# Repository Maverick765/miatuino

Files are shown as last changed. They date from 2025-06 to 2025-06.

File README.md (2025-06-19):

# Miatuino ECU NA6 PNP


MiatuinoはSpeeduinoをベースとしたNA6ロードスター専用ECUプロジェクトです。

Speeduino MX-5 PNPモデルをベースとし、部品の入手性、組み立てやすさなどを改善しました。

基本的な技術情報については公式のWikiを参照してください。
https://wiki.speeduino.com

また、部品に関してはできる限り日本国内で入手しやすいものにしています。国内で入手できないものはAliexpressやLCSCで入手可能です。

---

## 対応車種

- 車種：ユーノス・ロードスター（NA6CE）
- 年式：1989年〜1995年
- エンジン：1.6L B6ZE(RS)

注意：NA8には対応していません。

---

## Speeduinoからの変更点

- Arduino Mega2560をMega2560 Proに変更
- SMD部品を減らし、手はんだで組み立てやすいように変更
- A/C制御回路の追加
- 電源回路をROHM製のDC-DCコンバータBP5293-50に変更
- MAPセンサをBOSCH製0 281 002 593に変更

---

## 注意事項

- 仕様はほぼSpeeduinoと同様です。詳細仕様は [Speeduino公式Wiki](https://wiki.speeduino.com/) を参照してください。
- 純正には**吸気温センサー（IAT）が存在しない**ため、追加設置が必須です。
- ノック制御、スピードセンサーなどには非対応です。

---

## ECUの組み立てと取付に必要なもの

- Miatuino基板  
リポジトリ内のGerberファイルを利用。
- 実装用部品  
リポジトリ内の部品表を参照。
- 吸気温センサー(IAT)  
品番：25036751  
エアフロメーターを外したカプラに接続します。  
Aliexpressなどで入手可能
- 吸気温センサー用カプラ  
Aliexpressで「7pin Automotive Connector」などと検索すれば見つかります。
- スロットルポジションセンサー(TPS)  
品番：0280122001  
カプラの形状と配線が純正と同じため、そのまま利用できます。  
Aliexpressなどで入手可能。
- スロットルポジションセンサー用マウントアダプター  
リポジトリ内の.stlファイルを利用。  
3Dプリンタで出力するか、3Dプリントサービスを利用してください。  
.stlファイルは以下のページからも入手可能です。  
[1.6 Miata Kia type tps adapter M5 nuts](https://www.thingiverse.com/thing:4611603)
- MAPセンサー  
0 281 002 593  
Aliexpressなどで入手可能。
- MAPセンサー用カプラー  
品番：1928403966  
Aliexpressなどで入手可能。
- 基板用ケース  
基板のサイズは100mm x 100mmです。適当なサイズのアルミケースに入れます。
- 基板用USB Type Cコネクタ  
ケース内のMega 2560 Proと接続するためのパネルマウントのType Cコネクタ。
- 内径4.5mmのホース   
3m程度。キジマのガソリンホースがおススメです。
- TunerStudio  
[公式ページ](https://www.efianalytics.com/TunerStudio/)から入手可能。
- SpeedyLoader  
[公式ページ](https://speeduino.com/home/support/downloads)から入手可能。

---

## 製作

基本的にはKiCADのプロジェクトや部品表を見ながらはんだ付けすればOKです。
MAPセンサーは基板の3ピンコネクタにカプラを介して取り付けます。

---

## ファームウェアの書き込み

SpeedyLoaderを利用してファームウェアを書き込みます。
[SpeedyLoaderの公式マニュアル](https://wiki.speeduino.com/en/Installing_Firmware)を参考にしてください。

また、書き込みが完了したらbase tuneをダウンロードしておきます。

---

## 取付手順

### スロットルポジションセンサーを交換する

純正のスロットルポジションセンサーを外し、新しいスロットルポジションセンサーをアダプターを利用して取り付けます。

なお、純正のセンサーを取り外すには、スロットルボディーを外す必要があります。
(純正のセンサーを破壊すればスロットルボディーを外さずに新しいセンサーを取り付けることも可能ですがおススメしません)

### エアフロメーターのカプラを外して吸気温センサーを取り付ける

エアフロメータにつながっている7ピンのカプラを外し、吸気温センサを取り付けます。

### ST-SIGのヒューズを外す

エンジンルーム内の運転席側のヒューズボックスを開け、ST-SIGのヒューズを外します。
なお、Miatuinoを利用する場合、このヒューズは常に外したままにしておく必要があります。

_ST-SIGのヒューズは、セルモーターを回している間、一時的に燃料ポンプを動かすための電源が来ているヒューズです。_
_純正状態のNA6では、燃料ポンプの電源ON/OFFをフラップ式のエアフロメータの中にある機械式の接点で行っています。つまり、エンジンが回って負圧が発生している状態でないと燃料ポンプは作動しません。_
_エンジン始動時は負圧が弱く、この接点が動かないため、一時的に燃料ポンプに電源を供給する必要があります。その電源が来ているのがST-SIGのヒューズです。_
_Miatuinoでは、エアフロメータの配線を流用して燃料ポンプの制御を行うことになりますが、この時、ST-SIGのヒューズを残したままにしていると、キーを回したときに基板のドライバICに電流が逆流し、基板が焼けます。_

### 純正ECUを取り外す

助手席側スカッフプレート、一部のトリムを外してカーペットをめくります。
スチールのカバーパネルを外すと、ステーで固定されたECUが見えるので取り外し、カプラーを外します。

### MAPセンサーへつなぐホースを通す

MiatuinoではDジェトロニック方式になるため、インテークマニホールドの負圧をホースでECUまで接続する必要があります。
純正のインテークマニホールドには、ゴムキャップが付いた使われていない負圧取り出しニップルがあるので、それを利用します。
また、ロードスターのエンジンルーム隔壁にはゴム栓でメクラされた穴があるので、その栓を外してホースを通します。

カーペットをめくっている間に、エンジンルーム側からホースを送り、室内側の足元まで届かせます。
室内と反対側のホースの先をインマニにあるニップルに取り付けます。

### Miatuinoを取り付ける

純正ECUを取り外したカプラと、先ほど通したホースをMiatuinoに繋ぎます。
ECUのセッティングやトラブルシューティングのためにも、ECUは元の場所に戻さず、助手席足元に転がすなりしておきます。
ECU底面に面ファスナーのテープを取り付け、内装に張り付けておくのもおすすめです。

---

## セットアップ手順

PCとMiatuinoをUSBケーブルで接続し、PCでTuner Studioを起動し、初期データの書き込みと各種センサーのキャリブレーションを行います。

#### 初期データの書き込み

SpeedyLoaderからダウンロードしたbase tuneを書き込みます。

[File] -> [Load Tune(MSQ)]を選択して、SpeedyLoaderでからダウンロードしたbase tuneを書き込みます。

#### TPSのキャリブレーション

[Tools] -> [Calibrate TPS]を選択します。

正しくTPSが接続されていれば、アクセルペダルを踏めば値が変化することを確認できます。

まずはアクセルを完全に戻した状態で[Closed throttle ADC Count]の右の[Get Current]をクリックして、スロットル全閉時の値を取得します。
次に、アクセルを完全に踏み込んだ状態で[Full throttle ADC Count]の右の[Get Current]をクリックして、スロットル前回時の値を取得します。
完了したら[Accept]をクリックします。

この際、センサーの極性(全開で0Vか、全閉で0Vか)で警告が出ることがありますが、そのまま進めればSpeeduino側で勝手に極性を変更してくれます。

#### 水温センサーのキャリブレーション

[Tools] -> [Calibrate Tempereture Sensor]を選択します。

[SensorTable]のプルダウンから[Coolant Tempereture Sensor]を選択します。

[Table Input Solution]が3 Point Therm Generatorになっていることを確認します。

[Common Sensor Values]のプルダウンから[RX7_CLT(S4&S5)]を選択します。

[Write to Controller]をクリックして完了したら[Close]をクリックします。

#### 吸気温センサーのキャリブレーション

[Tools] -> [Calibrate Tempereture Sensor]を選択します。

[SensorTable]のプルダウンから[Air Tempereture Sensor]を選択します。

[Table Input Solution]が3 Point Therm Generatorになっていることを確認します。

[Common Sensor Values]のプルダウンから[RX7_AFM(S5 in AFM)]を選択します。

[Write to Controller]をクリックして完了したら[Close]をクリックします。

#### O2センサーの設定

[Tuning] -> [AFR/O2]を選択します。

純正のO2センサーを利用する場合、[Sensor Type]に[Narrow Band]を指定します。

完了したら[Burn]をクリックして[Close]をクリックします。

純正のO2センサーを利用する場合はこれで完了ですが、社外のワイドバンドセンサーを付けている場合はキャリブレーションを行う必要があります。

[Tools] -> [Calibrate AFR Sensor]を選択します。

[EGO Sensor]のプルダウンメニューから、利用しているセンサーのメーカーを選択します。

[Write to Controller]をクリックして完了したら[Close]をクリックします。

---

## 関連リンク

- [Speeduino 公式サイト（英語）](https://speeduino.com/)
- [Speeduino Wiki（英語）](https://wiki.speeduino.com/en/boards/MX5_PNP)
- [TunerStudio ダウンロードページ](https://www.efianalytics.com/TunerStudio/)
- [Speedy Loader ダウンロードページ](https://speeduino.com/home/support/downloads)
- [1.6 Miata Kia type tps adapter M5 nuts](https://www.thingiverse.com/thing:4611603)

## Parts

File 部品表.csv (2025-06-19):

Reference | Value | URL | 数量 | 備考
C1,C3 | 10uF | https://akizukidenshi.com/catalog/g/g117897/ | 2
C2,C6,C7,C8,C11,C12,C13,C17,C18,C19,C20,C21,C22,C23 | 0.1uF | https://akizukidenshi.com/catalog/g/g117059/ | 14
C4 | 22uF | https://akizukidenshi.com/catalog/g/g108156/ | 1
C5 | 470pf | https://akizukidenshi.com/catalog/g/g108130/ | 1
C9,C10,C14,C15,C16 | 0.22uF | https://akizukidenshi.com/catalog/g/g103096/ | 5
D1 | 1N5818 | https://www.lcsc.com/product-detail/Schottky-Diodes_STMicroelectronics-1N5818_C5220773.html?s_z=n_1N5818 | 1
D2 | SBM245L | https://akizukidenshi.com/catalog/g/g117439/ | 1
D3 | LED Power | https://akizukidenshi.com/catalog/g/g111637/ | 1
D4,D5,D6,D8,D13,D14,D19,D20 | D | https://akizukidenshi.com/catalog/g/g100941/ | 8
D7 | LED Fuel | https://akizukidenshi.com/catalog/g/g111577/ | 1
D9,D10,D11,D12,D15,D16,D17,D18 | LED Inj, LED Ign | https://akizukidenshi.com/catalog/g/g112607/ | 8
J1 | Connector_174917-1 | https://www.lcsc.com/product-detail/Wire-To-Board-Connector_TE-Connectivity-174917-1_C5166285.html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 | 1 | 入手性にやや難あり。 「174917-1」で検索すると見つかるかも。
J2 | Conn_01x03_Socket | https://akizukidenshi.com/catalog/g/g112816/ | 1
R1,R6,R7,R8,R12,R13,R14,R44,R45 | 470R | https://akizukidenshi.com/catalog/g/g125471/ | 9
R2,R23 | 10k | https://akizukidenshi.com/catalog/g/g125103/ | 2
R3 | 120R | https://akizukidenshi.com/catalog/g/g125121/ | 1
R4,R9,R15,R16,R20,R21,R22,R25,R26,R28,R29,R32,R33,R34,R35,R38,R39,R40,R41,R46 | 1k | https://akizukidenshi.com/catalog/g/g125102/ | 19
R5 | 3.9k | https://akizukidenshi.com/catalog/g/g125392/ | 1
R10,R11,R27 | 2.49k | https://jp.rs-online.com/web/p/through-hole-resistors/7549032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 | 3
R17,R18 | 220R | https://akizukidenshi.com/catalog/g/g125221/ | 2
R19 | 22K | https://akizukidenshi.com/catalog/g/g125223/ | 1
R24,R30,R31,R47,R48 | 100k | https://akizukidenshi.com/catalog/g/g125104/ | 7
R36,R37,R42,R43 | 3.3k | https://akizukidenshi.com/catalog/g/g125332/ | 4
RN1,RN2 | 100k | https://lcsc.com/product-detail/image/A05-104JP_C11398.html
RN3 | 3k | https://lcsc.com/product-detail/image/A05-302JP_C56024.html | 1
RV1 | Varistor | https://lcsc.com/product-detail/Varistors_RUILON-Shenzhen-Ruilongyuan-Elec-14D220K_C43370767.html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 | 1
SW1 | SW_Slide | https://akizukidenshi.com/catalog/g/g115643/ | 1
U1 | Mega 2560 Pro | Mega 2560 Pro | 1 | Aliexpressなどで入手可能。
U2 | IC_Automotive_MC33814 | https://lcsc.com/product-detail/Power-Management-Specialized_NXP-Semicon-MC33814AER2_C729078.html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 | 1
U3 | BP5293-50 | https://akizukidenshi.com/catalog/g/g111188/ | 1
U4 | KP234XTMA1 | https://www.lcsc.com/product-detail/Pressure-Sensors_Infineon-Technologies-KP234XTMA1_C3239348.html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 | 1
U5 | SP720 | https://www.lcsc.com/product-detail/ESD-and-Surge-Protection-TVS-ESD_Littelfuse-SP720ABG_C5299847.html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 | 1
U6,U8,U9,U11 | VNLD5090 | https://www.lcsc.com/product-detail/Power-Distribution-Switches_STMicroelectronics-VNLD5090TR-E_C222209.html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 | 4
U7 | VN5160S-E | https://www.lcsc.com/product-detail/Power-Distribution-Switches_STMicroelectronics-VN5160S-E_C262998.html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 | 1
U10,U12 | TC4424A | https://www.lcsc.com/product-detail/Gate-Drivers_Microchip-Tech-TC4424AVOA_C636876.html?s_z=n_TC4424A | 2
U13,U14 | TLP241A | https://akizukidenshi.com/catalog/g/g111516/ | 2

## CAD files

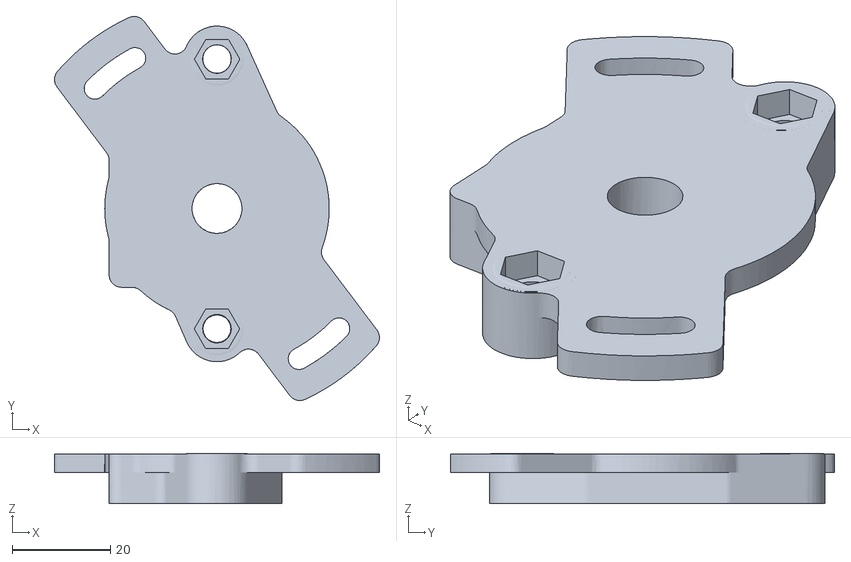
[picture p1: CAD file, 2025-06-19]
1.6_Miata_Kia_Tps_Adapter_M5.stl
66.3 x 78.3 x 10.2

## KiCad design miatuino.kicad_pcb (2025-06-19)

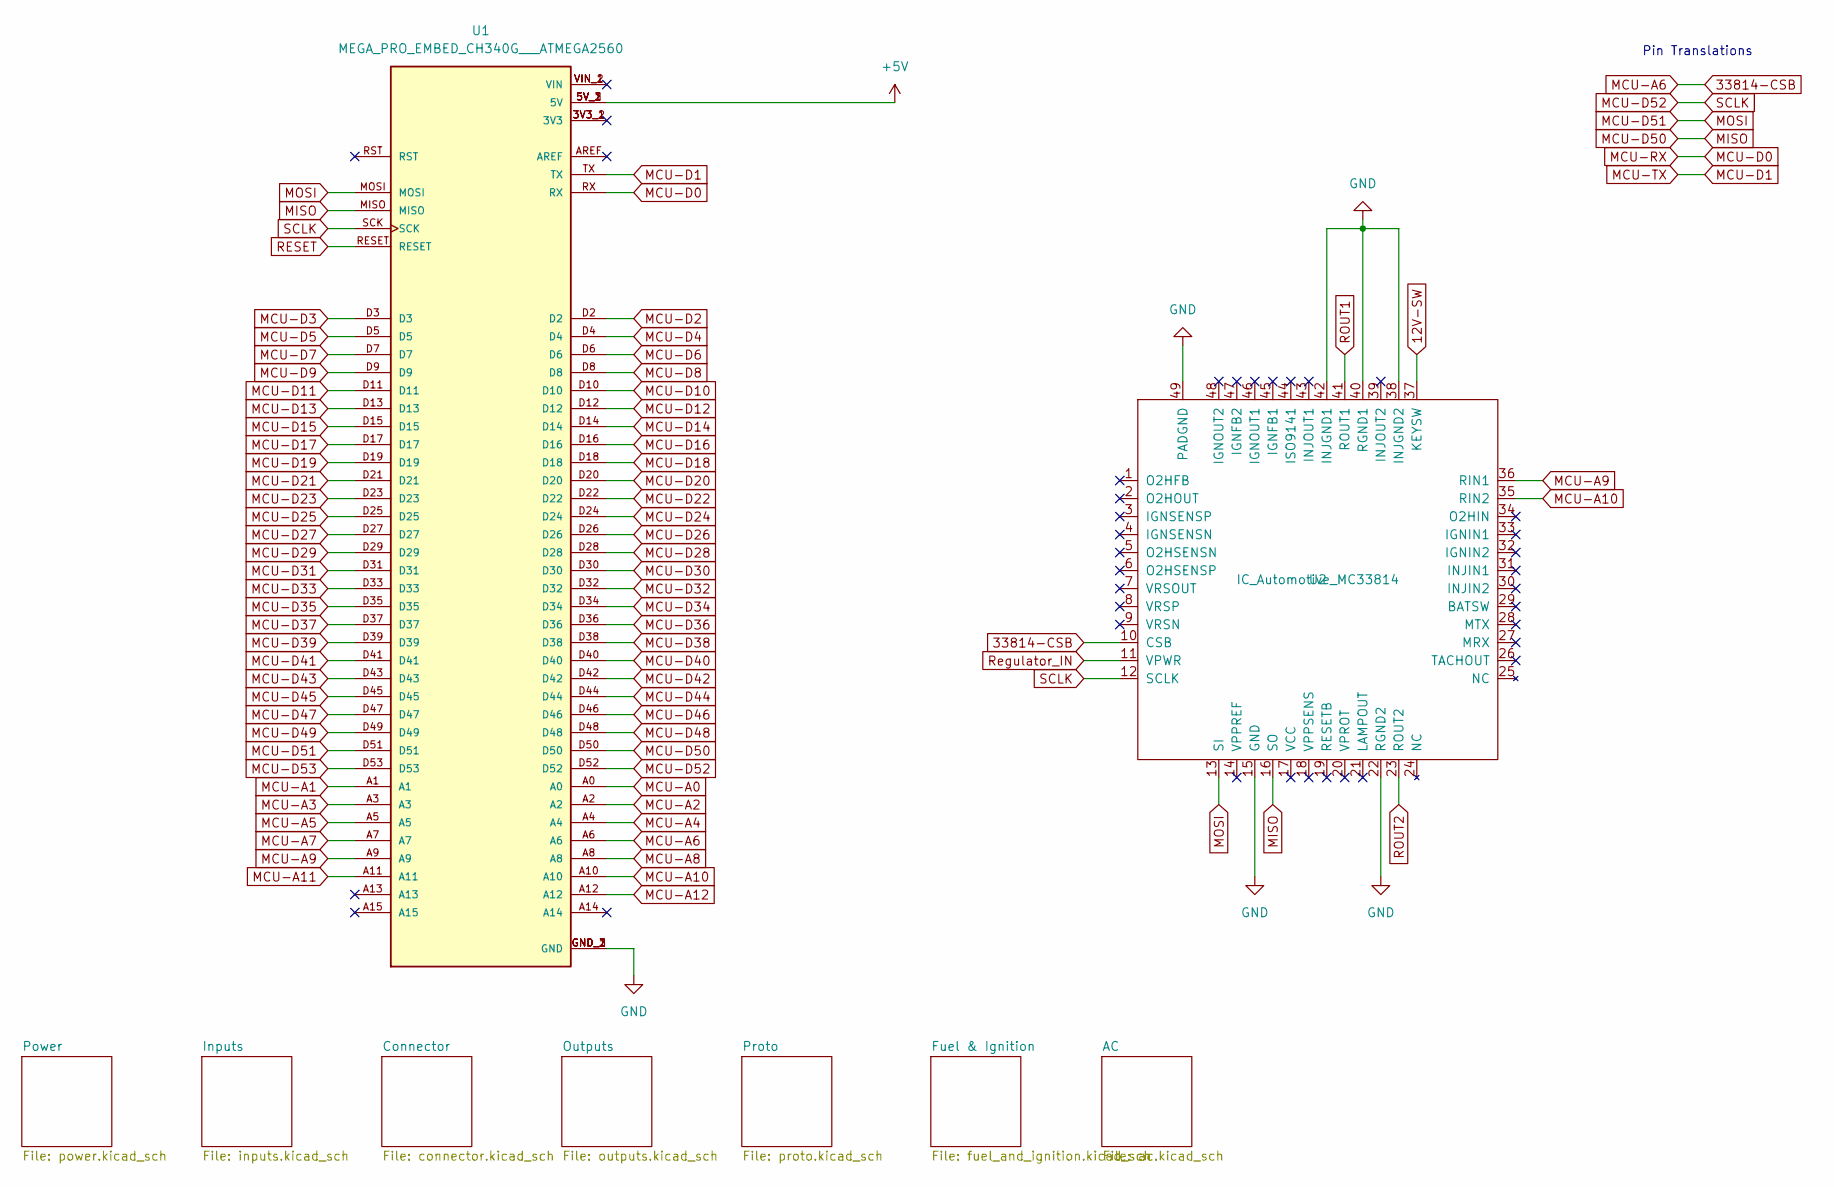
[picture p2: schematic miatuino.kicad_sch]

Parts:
U1: MEGA_PRO_EMBED_CH340G___ATMEGA2560; Arduino Mega Pro; PARTREV 12/May/2017
U2: IC_Automotive_MC33814; LQFP-48-1EP_7x7mm_P0.5mm_EP3.6x3.6mm_ThermalVias; Manufacturer_Part_Number MC33814

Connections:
12V-SW: U2.37 (KEYSW); also elsewhere on the board
33814-CSB: U1.A6, U2.10 (CSB)
+5V: U1.5V_1 (5V), U1.5V_2 (5V), U1.5V_3 (5V); also elsewhere on the board
ADC-Clamp-1: U1.A0; also elsewhere on the board
ADC-Clamp-2: U1.A1; also elsewhere on the board
ADC-Clamp-3: U1.A2; also elsewhere on the board
ADC-Clamp-4: U1.A3; also elsewhere on the board
ADC-Clamp-5: U1.A4; also elsewhere on the board
ADC-Clamp-11: U1.D12; also elsewhere on the board
ADC-Clamp-13: U1.D18; also elsewhere on the board
ADC-Clamp-14: U1.D19; also elsewhere on the board
GND: U1.GND_1 (GND), U1.GND_2 (GND), U1.GND_3 (GND), U2.15 (GND), U2.22 (RGND2), U2.38 (INJGND2), U2.40 (RGND1), U2.42 (INJGND1), U2.49 (PADGND); also elsewhere on the board
MCU-A5: U1.A5; also elsewhere on the board
MCU-A7: U1.A7
MCU-A8: U1.A8
MCU-A9: U1.A9, U2.36 (RIN1)
MCU-A10: U1.A10, U2.35 (RIN2)
MCU-A11: U1.A11
MCU-A12: U1.A12; also elsewhere on the board
MCU-D0: U1.RX; also elsewhere on the board
MCU-D1: U1.TX; also elsewhere on the board
MCU-D2: U1.D2; also elsewhere on the board
MCU-D3: U1.D3
MCU-D4: U1.D4; also elsewhere on the board
MCU-D5: U1.D5
MCU-D6: U1.D6
MCU-D7: U1.D7
MCU-D8: U1.D8; also elsewhere on the board
MCU-D9: U1.D9; also elsewhere on the board
MCU-D10: U1.D10; also elsewhere on the board
MCU-D11: U1.D11; also elsewhere on the board
MCU-D13: U1.D13
MCU-D14: U1.D14
MCU-D15: U1.D15
MCU-D16: U1.D16
MCU-D17: U1.D17
MCU-D20: U1.D20; also elsewhere on the board
MCU-D21: U1.D21
MCU-D22: U1.D22
MCU-D23: U1.D23
MCU-D24: U1.D24
MCU-D25: U1.D25
MCU-D26: U1.D26
MCU-D27: U1.D27
MCU-D28: U1.D28
MCU-D29: U1.D29
MCU-D30: U1.D30
MCU-D31: U1.D31
MCU-D32: U1.D32; also elsewhere on the board
MCU-D33: U1.D33; also elsewhere on the board
MCU-D34: U1.D34
MCU-D35: U1.D35; also elsewhere on the board
MCU-D36: U1.D36
MCU-D37: U1.D37; also elsewhere on the board
MCU-D38: U1.D38
MCU-D39: U1.D39; also elsewhere on the board
MCU-D40: U1.D40
MCU-D41: U1.D41; also elsewhere on the board
MCU-D42: U1.D42
MCU-D43: U1.D43
MCU-D44: U1.D44; also elsewhere on the board
MCU-D45: U1.D45
MCU-D46: U1.D46; also elsewhere on the board
MCU-D47: U1.D47
MCU-D48: U1.D48
MCU-D49: U1.D49; also elsewhere on the board
MCU-D50: U1.D50, U1.MISO, U2.16 (SO)
MCU-D51: U1.D51, U1.MOSI, U2.13 (SI)
MCU-D52: U1.D52, U1.SCK, U2.12 (SCLK)
MCU-D53: U1.D53
RESET: U1.RESET; also elsewhere on the board
ROUT1: U2.41 (ROUT1); also elsewhere on the board
ROUT2: U2.23 (ROUT2)
Regulator_IN: U2.11 (VPWR); also elsewhere on the board

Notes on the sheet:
Pin Translations

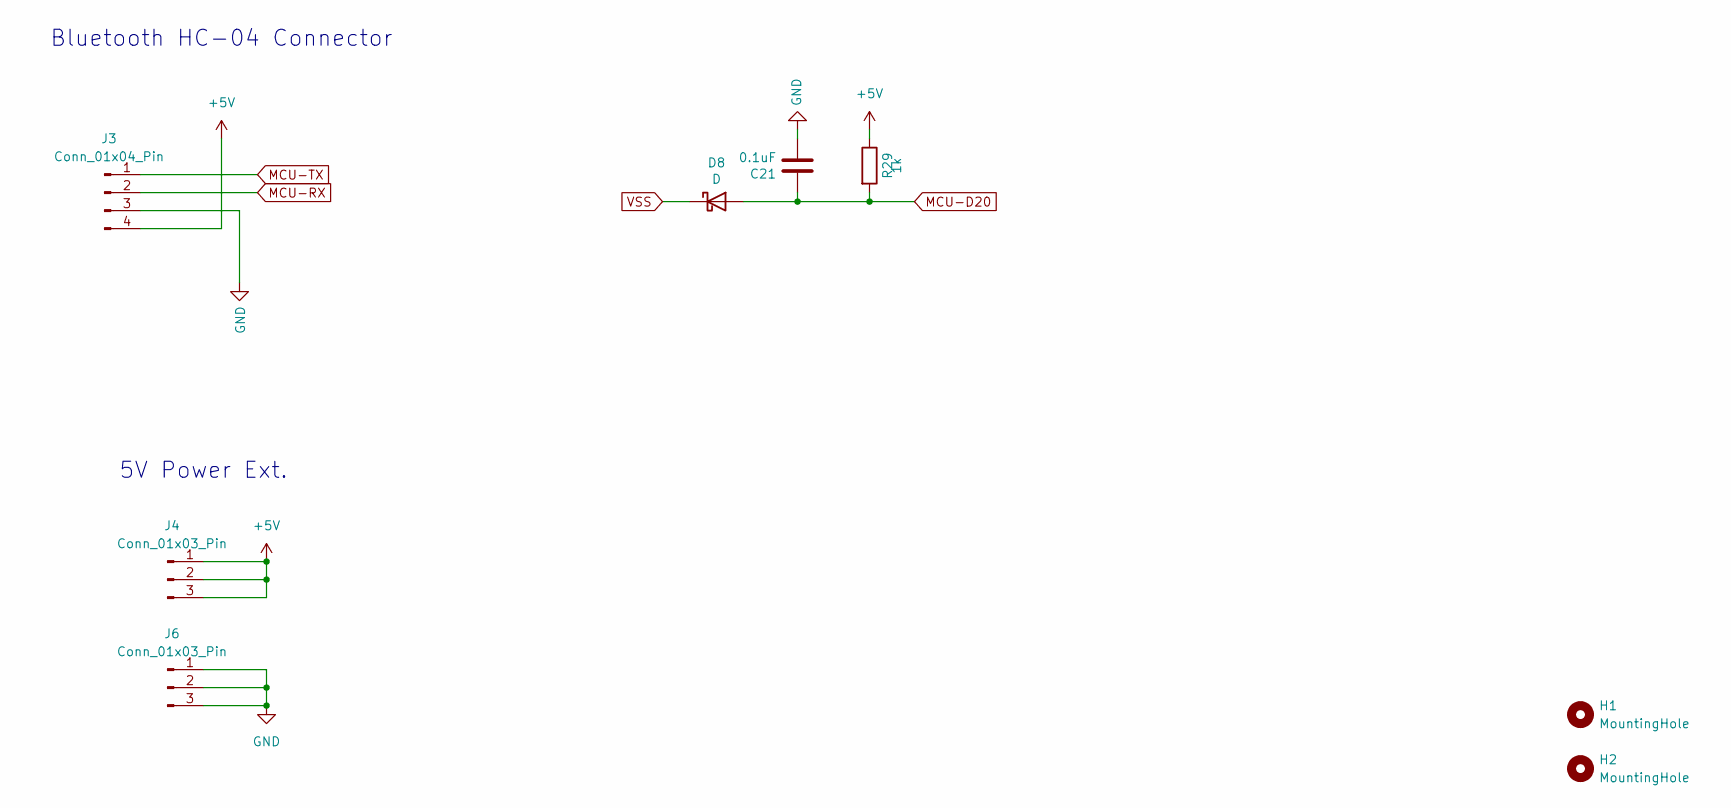
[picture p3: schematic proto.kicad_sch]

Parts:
C21: 0.1uF; C_Disc_D4.7mm_W2.5mm_P5.00mm; Manufacturer_Part_Number CC0805KRX7R9BB104; Digikey Part Number 311-1140-1-ND
D8: D; D_T-1_P5.08mm_Horizontal; Manufacturer_Part_Number 1N4448WX-TP; Digikey Part Number 1N4448WXTPMSCT-ND
H1, H2: MountingHole; MountingHole_3.2mm_M3_DIN965_Pad
J3: Conn_01x04_Pin; PinSocket_1x04_P2.54mm_Vertical
J4, J6: Conn_01x03_Pin; PinHeader_1x03_P2.54mm_Vertical
R29: 1k; R_Axial_DIN0207_L6.3mm_D2.5mm_P7.62mm_Horizontal; Manufacturer_Part_Number RC0805FR-071KL; Digikey Part Number 311-1.00KCRCT-ND

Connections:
+5V: J3.4, J4.1, J4.2, J4.3, R29.1; also elsewhere on the board
GND: C21.2, J3.3, J6.1, J6.2, J6.3; also elsewhere on the board
MCU-D0: J3.2; also elsewhere on the board
MCU-D1: J3.1; also elsewhere on the board
MCU-D20: C21.1, D8.2 (A), R29.2; also elsewhere on the board
VSS: D8.1 (K); also elsewhere on the board

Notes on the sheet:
Bluetooth HC-04 Connector
5V Power Ext.

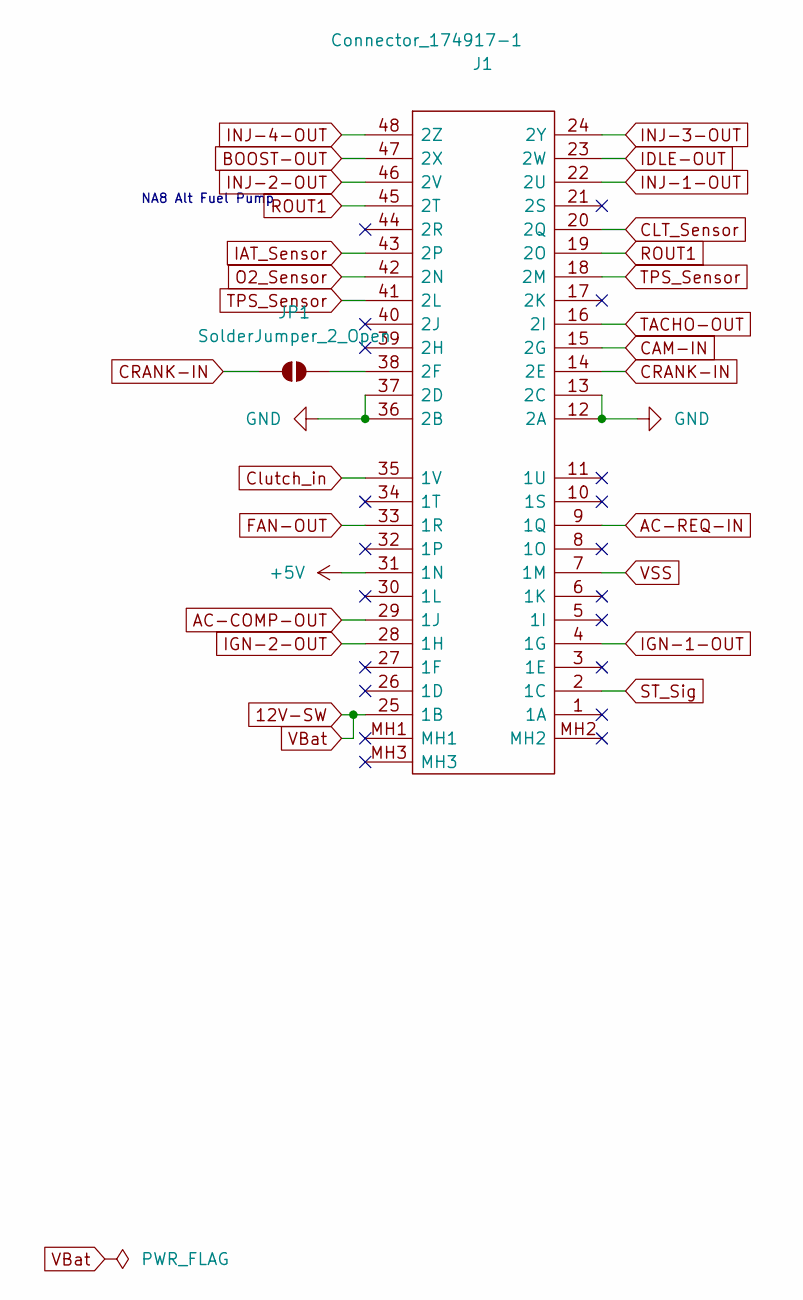
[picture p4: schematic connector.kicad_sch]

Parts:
J1: Connector_174917-1; 1749171; Manufacturer_Part_Number 174917-1
JP1: SolderJumper_2_Open; SolderJumper-2_P1.3mm_Open_RoundedPad1.0x1.5mm

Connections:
12V-SW: J1.25 (1B); also elsewhere on the board
+5V: J1.31 (1N); also elsewhere on the board
AC-COMP-OUT: J1.29 (1J); also elsewhere on the board
AC-REQ-IN: J1.9 (1Q); also elsewhere on the board
BOOST-OUT: J1.47 (2X); also elsewhere on the board
CAM-IN: J1.15 (2G); also elsewhere on the board
CLT_Sensor: J1.20 (2Q); also elsewhere on the board
CRANK-IN: J1.14 (2E), JP1.1 (A); also elsewhere on the board
Clutch_in: J1.35 (1V); also elsewhere on the board
FAN-OUT: J1.33 (1R); also elsewhere on the board
GND: J1.12 (2A), J1.13 (2C), J1.36 (2B), J1.37 (2D); also elsewhere on the board
IAT_Sensor: J1.43 (2P); also elsewhere on the board
IDLE-OUT: J1.23 (2W); also elsewhere on the board
IGN-1-OUT: J1.4 (1G); also elsewhere on the board
IGN-2-OUT: J1.28 (1H); also elsewhere on the board
INJ-1-OUT: J1.22 (2U); also elsewhere on the board
INJ-2-OUT: J1.46 (2V); also elsewhere on the board
INJ-3-OUT: J1.24 (2Y); also elsewhere on the board
INJ-4-OUT: J1.48 (2Z); also elsewhere on the board
unnamed: J1.38 (2F), JP1.2 (B)
O2_Sensor: J1.42 (2N); also elsewhere on the board
ROUT1: J1.19 (2O), J1.45 (2T); also elsewhere on the board
ST_Sig: J1.2 (1C); also elsewhere on the board
TACHO-OUT: J1.16 (2I); also elsewhere on the board
TPS_Sensor: J1.18 (2M), J1.41 (2L); also elsewhere on the board
VSS: J1.7 (1M); also elsewhere on the board

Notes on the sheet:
NA8 Alt Fuel Pump

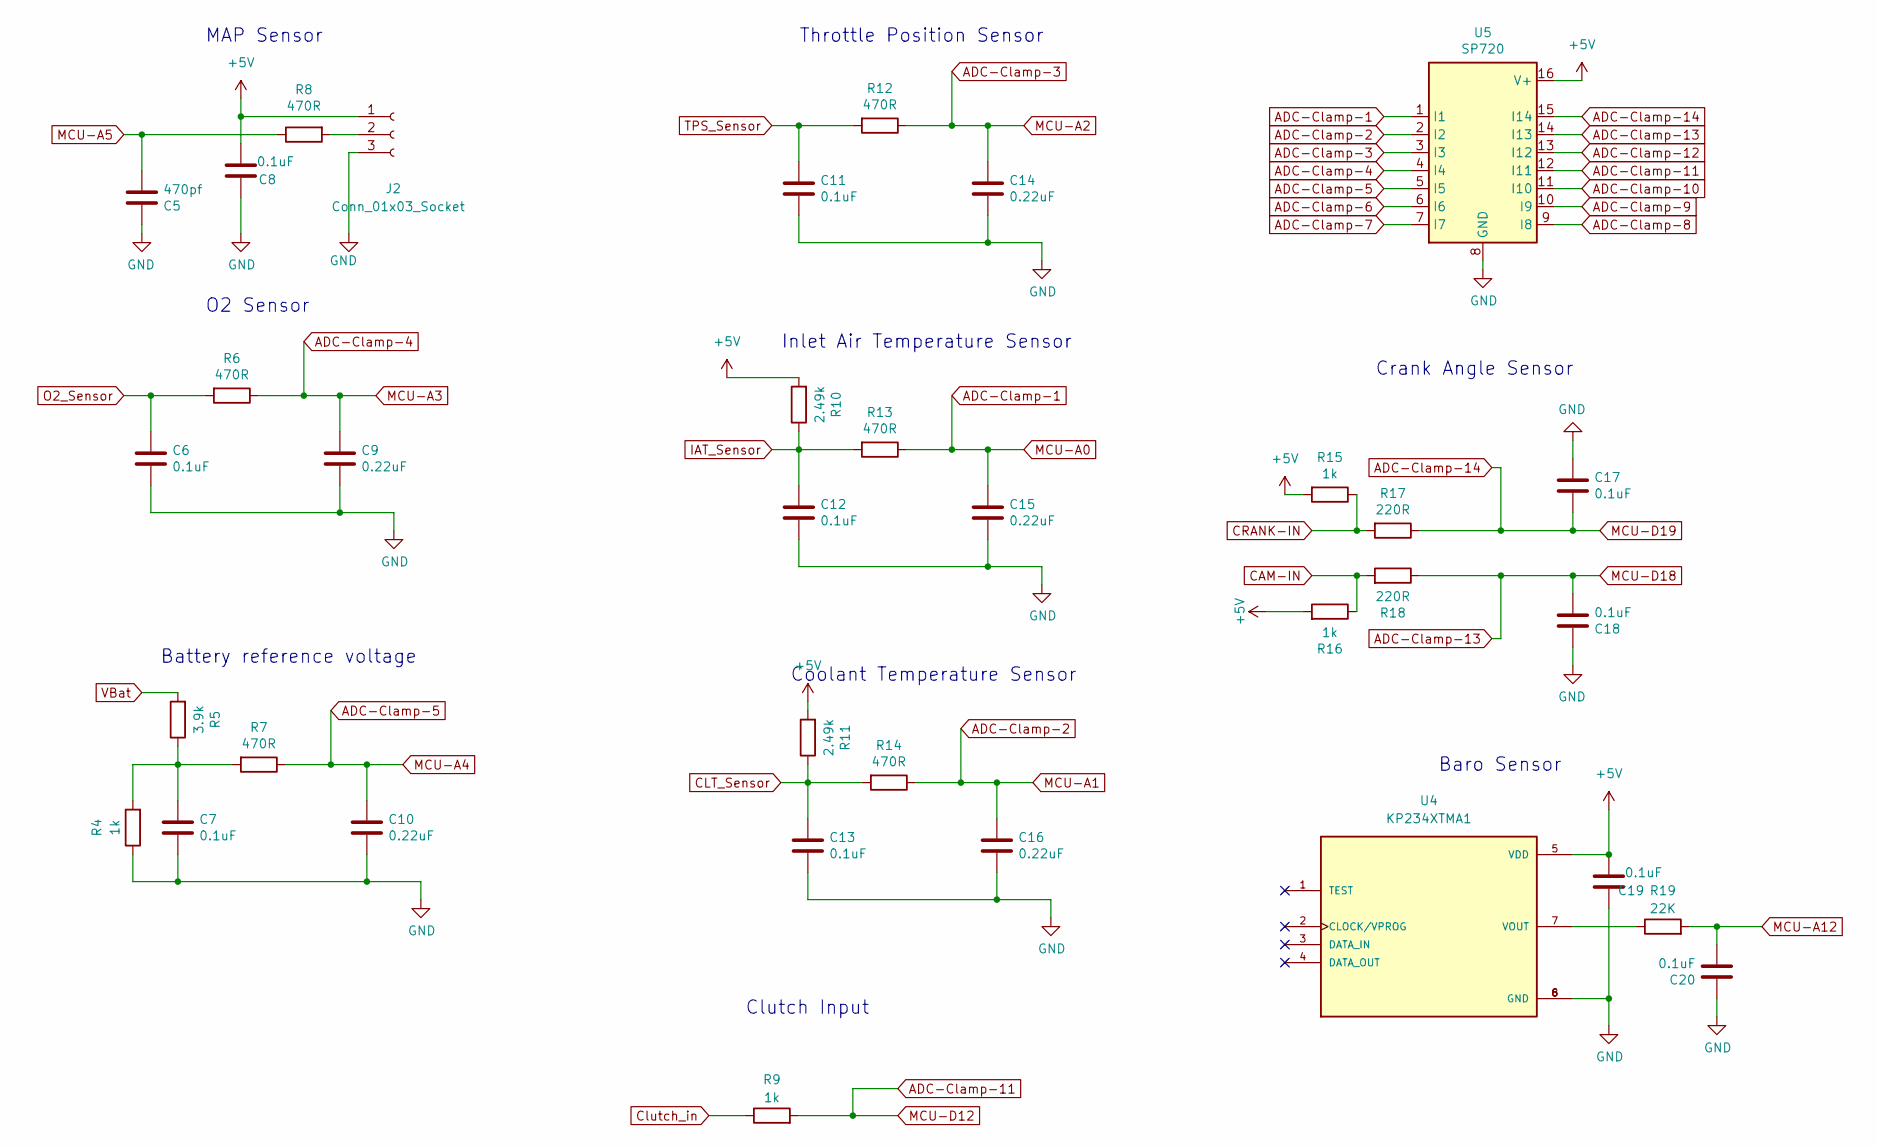
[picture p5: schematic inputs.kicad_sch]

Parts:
C5: 470pf; C_Disc_D4.7mm_W2.5mm_P5.00mm; Part # CC0805KRX7R9BB471; Digikey Part Number 311-1124-1-ND
C6, C7, C12, C13, C17, C18, C20: 0.1uF; C_Disc_D4.7mm_W2.5mm_P5.00mm; Manufacturer_Part_Number CC0805KRX7R9BB104; Digikey Part Number 311-1140-1-ND
C8: 0.1uF; C_Disc_D4.7mm_W2.5mm_P5.00mm; Part # CC0805KRX7R9BB103; Digikey Part Number 311-1136-1-ND
C9, C10, C14, C15, C16: 0.22uF; C_Disc_D4.7mm_W2.5mm_P5.00mm; Manufacturer_Part_Number CL21B224KOCNNNC; Digikey Part Number 1276-1284-1-ND
C11: 0.1uF; C_Disc_D4.7mm_W2.5mm_P5.00mm; Part # CC0805KRX7R9BB104; Digikey Part Number 311-1140-1-ND
C19: 0.1uF; C_Disc_D4.7mm_W2.5mm_P5.00mm; Manufacturer_Part_Number CC0805KRX7R9BB103; Digikey Part Number 311-1136-1-ND
J2: Conn_01x03_Socket; FanPinHeader_1x03_P2.54mm_Vertical
R4, R9, R15, R16: 1k; R_Axial_DIN0207_L6.3mm_D2.5mm_P7.62mm_Horizontal; Manufacturer_Part_Number RC0805FR-071KL; Digikey Part Number 311-1.00KCRCT-ND
R5: 3.9k; R_Axial_DIN0207_L6.3mm_D2.5mm_P7.62mm_Horizontal; Manufacturer_Part_Number RC0805FR-073K9L; Digikey Part Number 311-3.90KCRCT-ND
R6, R7, R12, R13, R14: 470R; R_Axial_DIN0207_L6.3mm_D2.5mm_P7.62mm_Horizontal; Manufacturer_Part_Number ERJ-6ENF4700V; Digikey Part Number P470CCT-ND
R8: 470R; R_Axial_DIN0207_L6.3mm_D2.5mm_P7.62mm_Horizontal; Part # ERJ-6ENF4700V; Digikey Part Number P470CCT-ND
R10, R11: 2.49k; R_Axial_DIN0207_L6.3mm_D2.5mm_P7.62mm_Horizontal; Manufacturer_Part_Number RT0805BRD072K49L; Digikey Part Number YAG1854CT-ND
R17, R18: 220R; R_Axial_DIN0207_L6.3mm_D2.5mm_P7.62mm_Horizontal; Manufacturer_Part_Number RC0805FR-07220RL; Digikey Part Number 311-220CRCT-ND
R19: 22K; R_Axial_DIN0207_L6.3mm_D2.5mm_P7.62mm_Horizontal; Manufacturer_Part_Number AC0805JR-0722KL; Digikey Part Number YAG3773CT-ND
U4: KP234XTMA1; XDCR_KP234XTMA1; PARTREV 1.0
U5: SP720; SOIC-16_3.9x9.9mm_P1.27mm; Manufacturer_Part_Number SP720ABTG; Digikey Part Number F3162CT-ND

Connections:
12V-SW: R5.2; also elsewhere on the board
+5V: C8.2, C19.2, J2.1, R10.2, R11.2, R15.2, R16.2, U4.5 (VDD), U5.16 (V+); also elsewhere on the board
ADC-Clamp-1: C15.1, R13.1, U5.1 (I1); also elsewhere on the board
ADC-Clamp-2: C16.1, R14.1, U5.2 (I2); also elsewhere on the board
ADC-Clamp-3: C14.1, R12.1, U5.3 (I3); also elsewhere on the board
ADC-Clamp-4: C9.1, R6.1, U5.4 (I4); also elsewhere on the board
ADC-Clamp-5: C10.1, R7.1, U5.5 (I5); also elsewhere on the board
ADC-Clamp-6: U5.6 (I6)
ADC-Clamp-7: U5.7 (I7)
ADC-Clamp-8: U5.9 (I8)
ADC-Clamp-9: U5.10 (I9)
ADC-Clamp-10: U5.11 (I10)
ADC-Clamp-11: R9.2, U5.12 (I11); also elsewhere on the board
ADC-Clamp-12: U5.13 (I12)
ADC-Clamp-13: C18.2, R18.1, U5.14 (I13); also elsewhere on the board
ADC-Clamp-14: C17.2, R17.1, U5.15 (I14); also elsewhere on the board
CAM-IN: R16.1, R18.2; also elsewhere on the board
CLT_Sensor: C13.1, R11.1, R14.2; also elsewhere on the board
CRANK-IN: R15.1, R17.2; also elsewhere on the board
Clutch_in: R9.1; also elsewhere on the board
GND: C5.1, C6.2, C7.2, C8.1, C9.2, C10.2, C11.2, C12.2, C13.2, C14.2, C15.2, C16.2, C17.1, C18.1, C19.1, C20.1, J2.3, R4.1, U4.6 (GND), U4.8 (GND), U5.8 (GND); also elsewhere on the board
IAT_Sensor: C12.1, R10.1, R13.2; also elsewhere on the board
MCU-A5: C5.2, R8.1; also elsewhere on the board
MCU-A12: C20.2, R19.2; also elsewhere on the board
unnamed: C7.1, R4.2, R5.1, R7.2
unnamed: J2.2, R8.2
unnamed: R19.1, U4.7 (VOUT)
O2_Sensor: C6.1, R6.2; also elsewhere on the board
TPS_Sensor: C11.1, R12.2; also elsewhere on the board

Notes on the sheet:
O2 Sensor
Coolant Temperature Sensor
Clutch Input
Crank Angle Sensor
Baro Sensor
Throttle Position Sensor
MAP Sensor
Battery reference voltage
Inlet Air Temperature Sensor

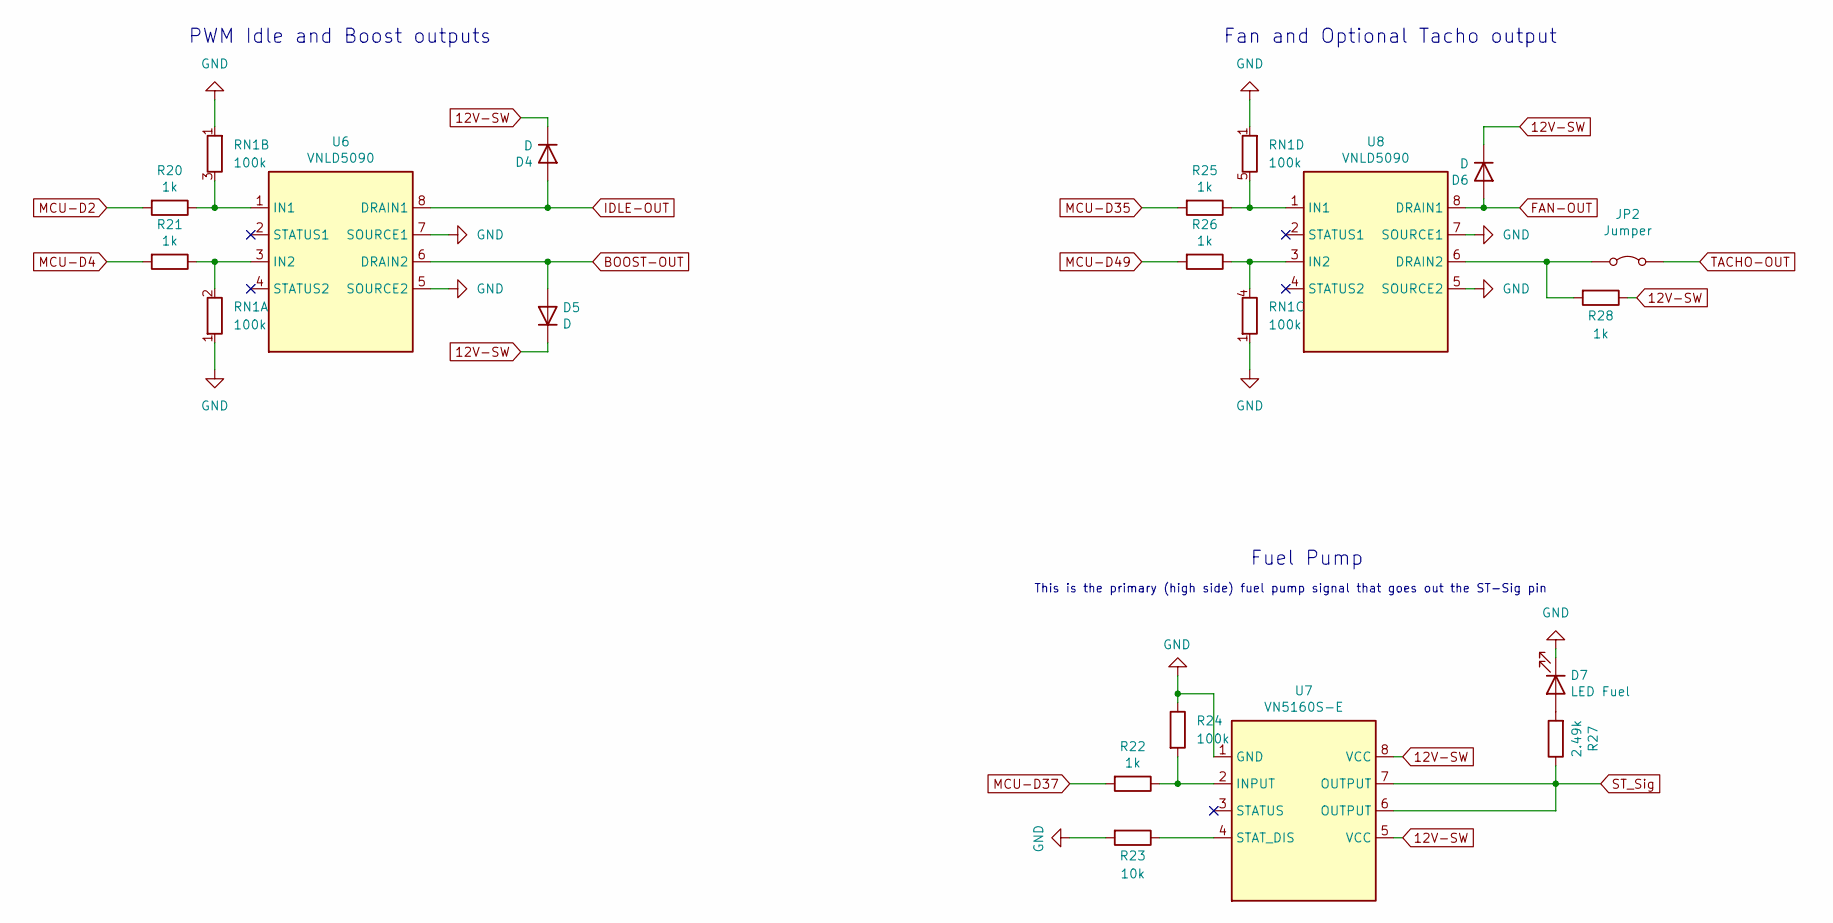
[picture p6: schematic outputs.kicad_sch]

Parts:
D4, D5, D6: D; D_DO-41_SOD81_P7.62mm_Horizontal; Manufacturer_Part_Number NBRS2H100T3G; Digikey Part Number NBRS2H100T3GTR-ND
D7: LED Fuel; LED_D3.0mm; Manufacturer_Part_Number LH R974-LP-1; Digikey Part Number 475-1415-1-ND
JP2: Jumper; SolderJumper-2_P1.3mm_Open_RoundedPad1.0x1.5mm
R20, R21, R22, R25, R26, R28: 1k; R_Axial_DIN0207_L6.3mm_D2.5mm_P7.62mm_Horizontal; Manufacturer_Part_Number RC0805FR-071KL; Digikey Part Number 311-1.00KCRCT-ND
R23: 10k; R_Axial_DIN0207_L6.3mm_D2.5mm_P7.62mm_Horizontal; Manufacturer_Part_Number RC0805JR-0710KL; Digikey Part Number 311-10KARCT-ND
R24: 100k; R_Axial_DIN0207_L6.3mm_D2.5mm_P7.62mm_Horizontal
R27: 2.49k; R_Axial_DIN0207_L6.3mm_D2.5mm_P7.62mm_Horizontal; Manufacturer_Part_Number RT0805BRD072K49L; Digikey Part Number YAG1854CT-ND
RN1: 100k; R_Array_SIP5
U6, U8: VNLD5090; SO-8_3.9x4.9mm_P1.27mm; Manufacturer_Part_Number VNLD5090-E; Digikey Part Number 497-18682-ND
U7: VN5160S-E; SO-8_3.9x4.9mm_P1.27mm; Manufacturer_Part_Number VN5160S-E; Digikey Part Number 497-19720-ND

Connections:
12V-SW: D4.1 (K), D5.1 (K), D6.1 (K), R28.1, U7.5 (VCC), U7.8 (VCC); also elsewhere on the board
BOOST-OUT: D5.2 (A), U6.6 (DRAIN2); also elsewhere on the board
FAN-OUT: D6.2 (A), U8.8 (DRAIN1); also elsewhere on the board
GND: D7.1 (K), R23.2, R24.1, RN1.1 (R1), U6.5 (SOURCE2), U6.7 (SOURCE1), U7.1 (GND), U8.5 (SOURCE2), U8.7 (SOURCE1); also elsewhere on the board
IDLE-OUT: D4.2 (A), U6.8 (DRAIN1); also elsewhere on the board
MCU-D2: R20.2; also elsewhere on the board
MCU-D4: R21.2; also elsewhere on the board
MCU-D35: R25.2; also elsewhere on the board
MCU-D37: R22.2; also elsewhere on the board
MCU-D49: R26.2; also elsewhere on the board
unnamed: D7.2 (A), R27.2
unnamed: JP2.1 (A), R28.2, U8.6 (DRAIN2)
unnamed: R21.1, RN1.2 (R1.2), U6.3 (IN2)
unnamed: R20.1, RN1.3 (R2.2), U6.1 (IN1)
unnamed: R26.1, RN1.4 (R3.2), U8.3 (IN2)
unnamed: R25.1, RN1.5 (R4.2), U8.1 (IN1)
unnamed: R22.1, R24.2, U7.2 (INPUT)
unnamed: R23.1, U7.4 (STAT_DIS)
ST_Sig: R27.1, U7.6 (OUTPUT), U7.7 (OUTPUT); also elsewhere on the board
TACHO-OUT: JP2.2 (B); also elsewhere on the board

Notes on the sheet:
Fan and Optional Tacho output
PWM Idle and Boost outputs
This is the primary (high side) fuel pump signal that goes out the ST-Sig pin
Fuel Pump

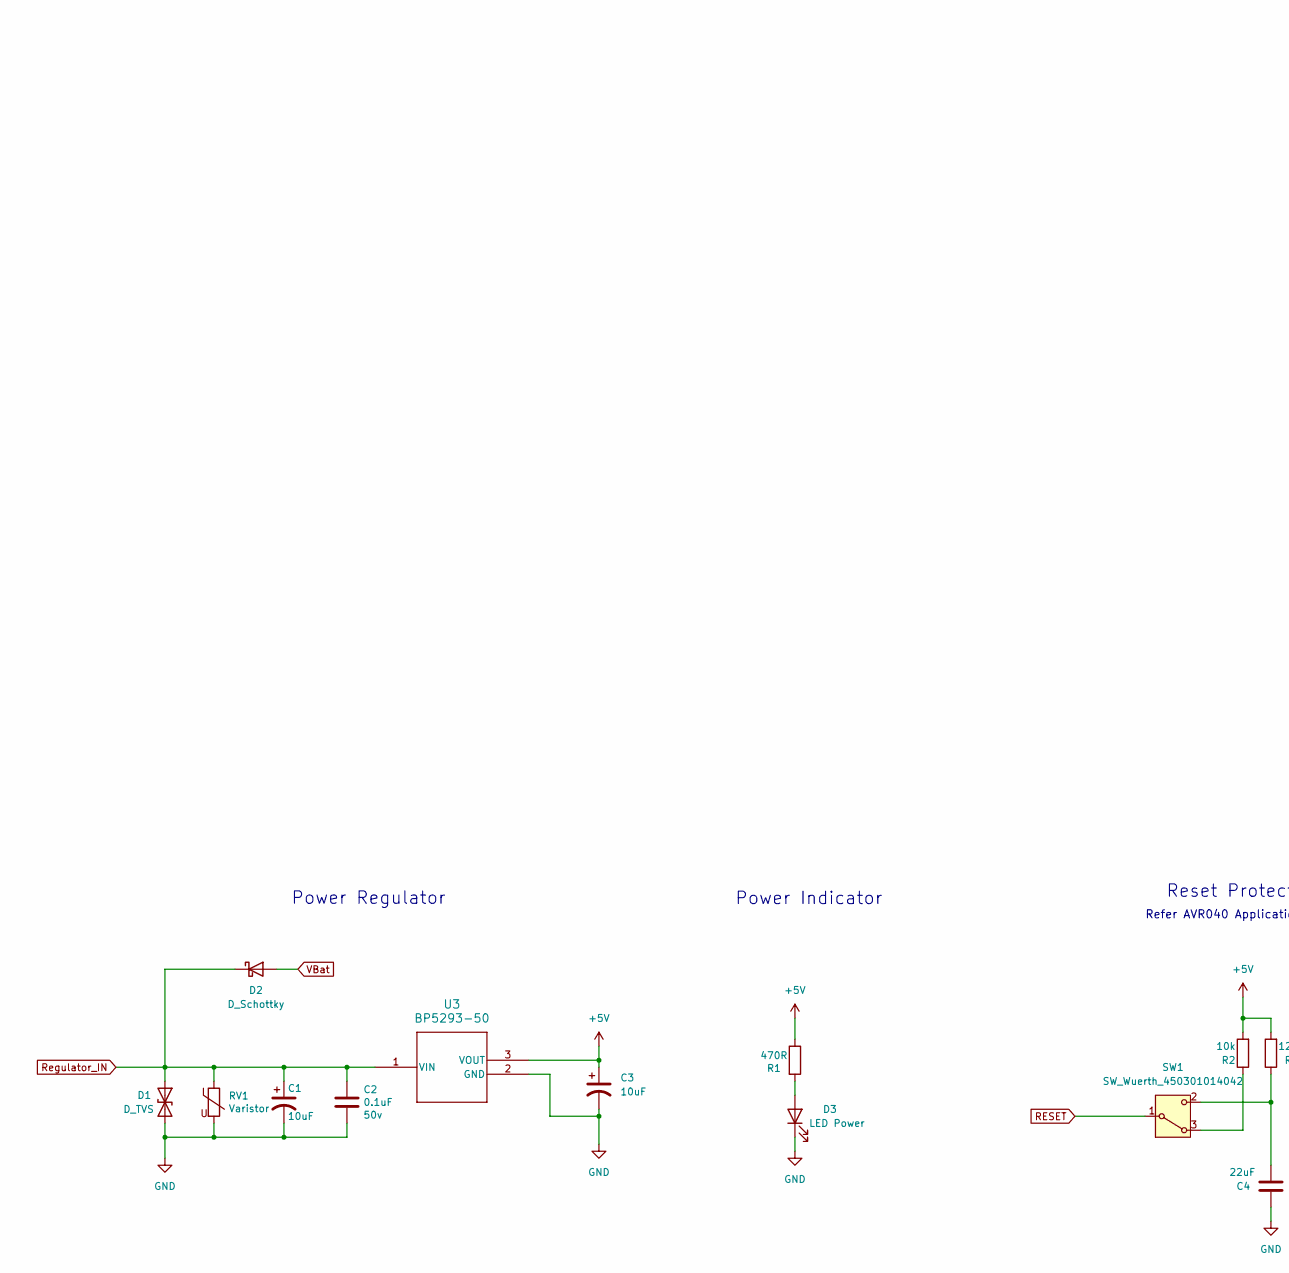
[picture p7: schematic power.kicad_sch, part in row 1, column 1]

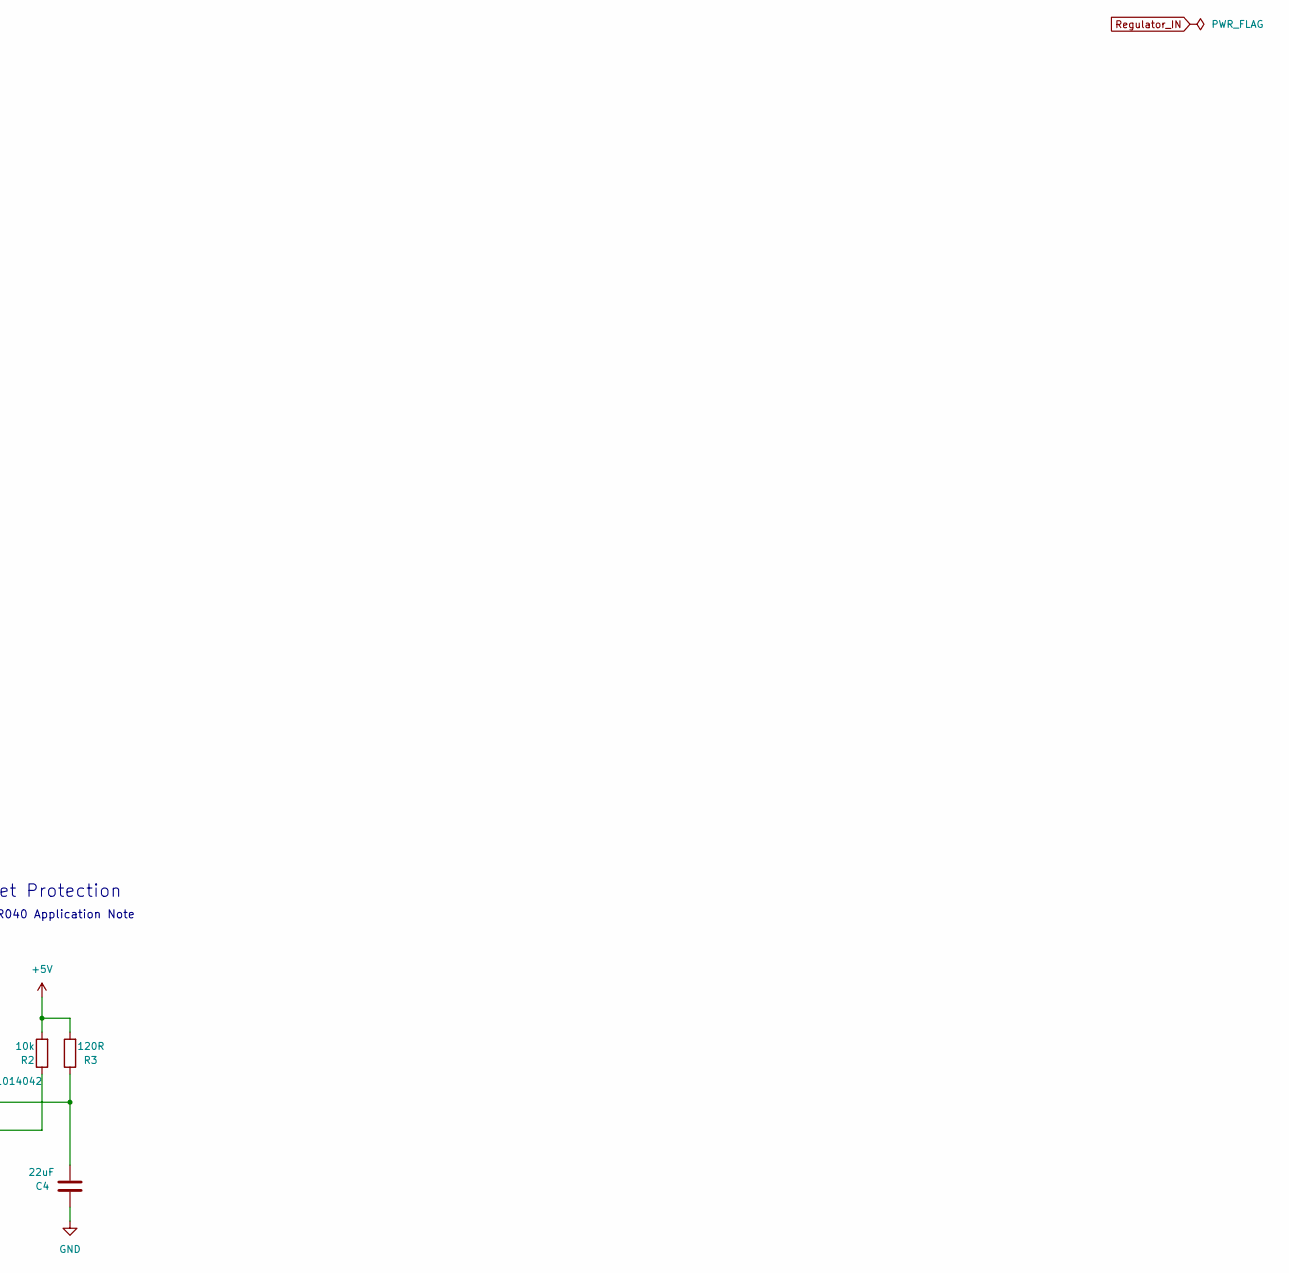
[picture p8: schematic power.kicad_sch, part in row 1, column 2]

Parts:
C1: 10uF; CP_Radial_D5.0mm_P2.00mm; Voltage 35v; Manufacturer_Part_Number T491D106K050AT; Digikey Part Number 399-8361-1-ND
C2: 0.1uF; C_Disc_D4.7mm_W2.5mm_P5.00mm; Voltage 50v; Manufacturer_Part_Number C1206C104K5RAC7867; Digikey Part Number 399-1249-1-ND
C3: 10uF; CP_Radial_D5.0mm_P2.00mm
C4: 22uF; C_Disc_D4.7mm_W2.5mm_P5.00mm; Manufacturer_Part_Number CL21A226KQCLRNC; Digikey Part Number 1276-6687-1-ND
D1: D_TVS; D_DO-41_SOD81_P7.62mm_Horizontal
D2: D_Schottky; D_DO-41_SOD81_P7.62mm_Horizontal; Manufacturer_Part_Number 1N5818-TP; Digikey Part Number 1N5818-TPCT-ND
D3: LED Power; LED_D3.0mm; Manufacturer_Part_Number LG R971-KN-1; Digikey Part Number 475-1410-1-ND
R1: 470R; R_Axial_DIN0207_L6.3mm_D2.5mm_P7.62mm_Horizontal; Manufacturer_Part_Number ERJ-6ENF4700V; Digikey Part Number P470CCT-ND
R2: 10k; R_Axial_DIN0207_L6.3mm_D2.5mm_P7.62mm_Horizontal; Manufacturer_Part_Number RC0805JR-0710KL; Digikey Part Number 311-10KARCT-ND
R3: 120R; R_Axial_DIN0207_L6.3mm_D2.5mm_P7.62mm_Horizontal; Manufacturer_Part_Number RC0805FR-07120RL; Digikey Part Number 311-120CRCT-ND
RV1: Varistor; RV_Disc_D15.5mm_W4.7mm_P7.5mm; Manufacturer_Part_Number MOV-14D220K; Digikey Part Number MOV-14D220K-ND
SW1: SW_Wuerth_450301014042; SW_Slide-03_Wuerth-WS-SLTV_10x2.5x6.4_P2.54mm
U3: BP5293-50

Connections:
12V-SW: D2.2 (A); also elsewhere on the board
+5V: C3.1, R1.1, R2.2, R3.2, U3.3 (VOUT); also elsewhere on the board
GND: C1.2, C2.2, C3.2, C4.2, D1.2 (A2), D3.1 (K), RV1.2, U3.2 (GND); also elsewhere on the board
unnamed: D3.2 (A), R1.2
unnamed: R2.1, SW1.3 (A)
unnamed: C4.1, R3.1, SW1.2 (C)
RESET: SW1.1 (B); also elsewhere on the board
Regulator_IN: C1.1, C2.1, D1.1 (A1), D2.1 (K), RV1.1, U3.1 (VIN); also elsewhere on the board

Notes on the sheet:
Power Regulator
Refer AVR040 Application Note
Power Indicator
Reset Protection

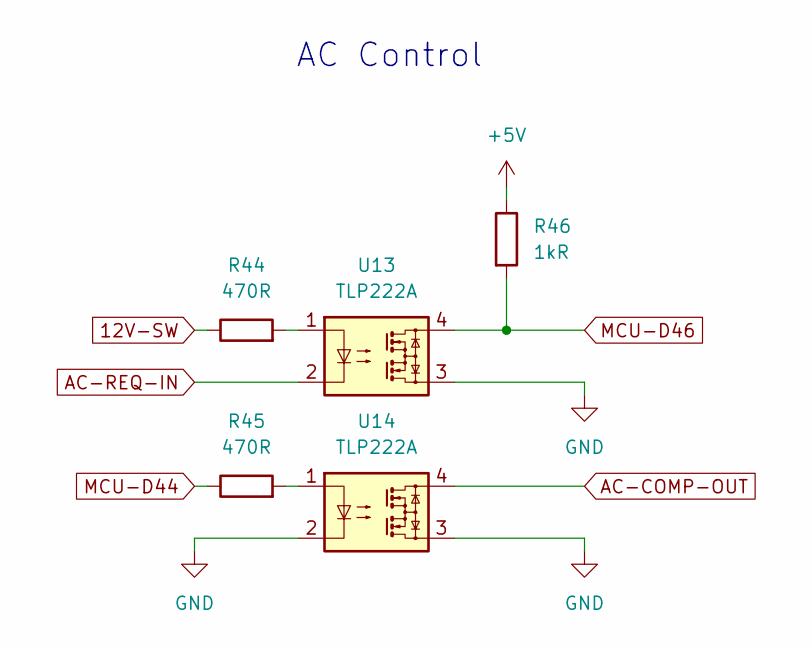
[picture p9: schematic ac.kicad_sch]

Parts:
R44, R45: 470R; R_Axial_DIN0207_L6.3mm_D2.5mm_P7.62mm_Horizontal
R46: 1kR; R_Axial_DIN0207_L6.3mm_D2.5mm_P7.62mm_Horizontal
U13, U14: TLP222A; DIP-4_W7.62mm

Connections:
12V-SW: R44.1; also elsewhere on the board
+5V: R46.1; also elsewhere on the board
AC-COMP-OUT: U14.4; also elsewhere on the board
AC-REQ-IN: U13.2; also elsewhere on the board
GND: U13.3, U14.2, U14.3; also elsewhere on the board
MCU-D44: R45.1; also elsewhere on the board
MCU-D46: R46.2, U13.4; also elsewhere on the board
unnamed: R44.2, U13.1
unnamed: R45.2, U14.1

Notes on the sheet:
AC Control

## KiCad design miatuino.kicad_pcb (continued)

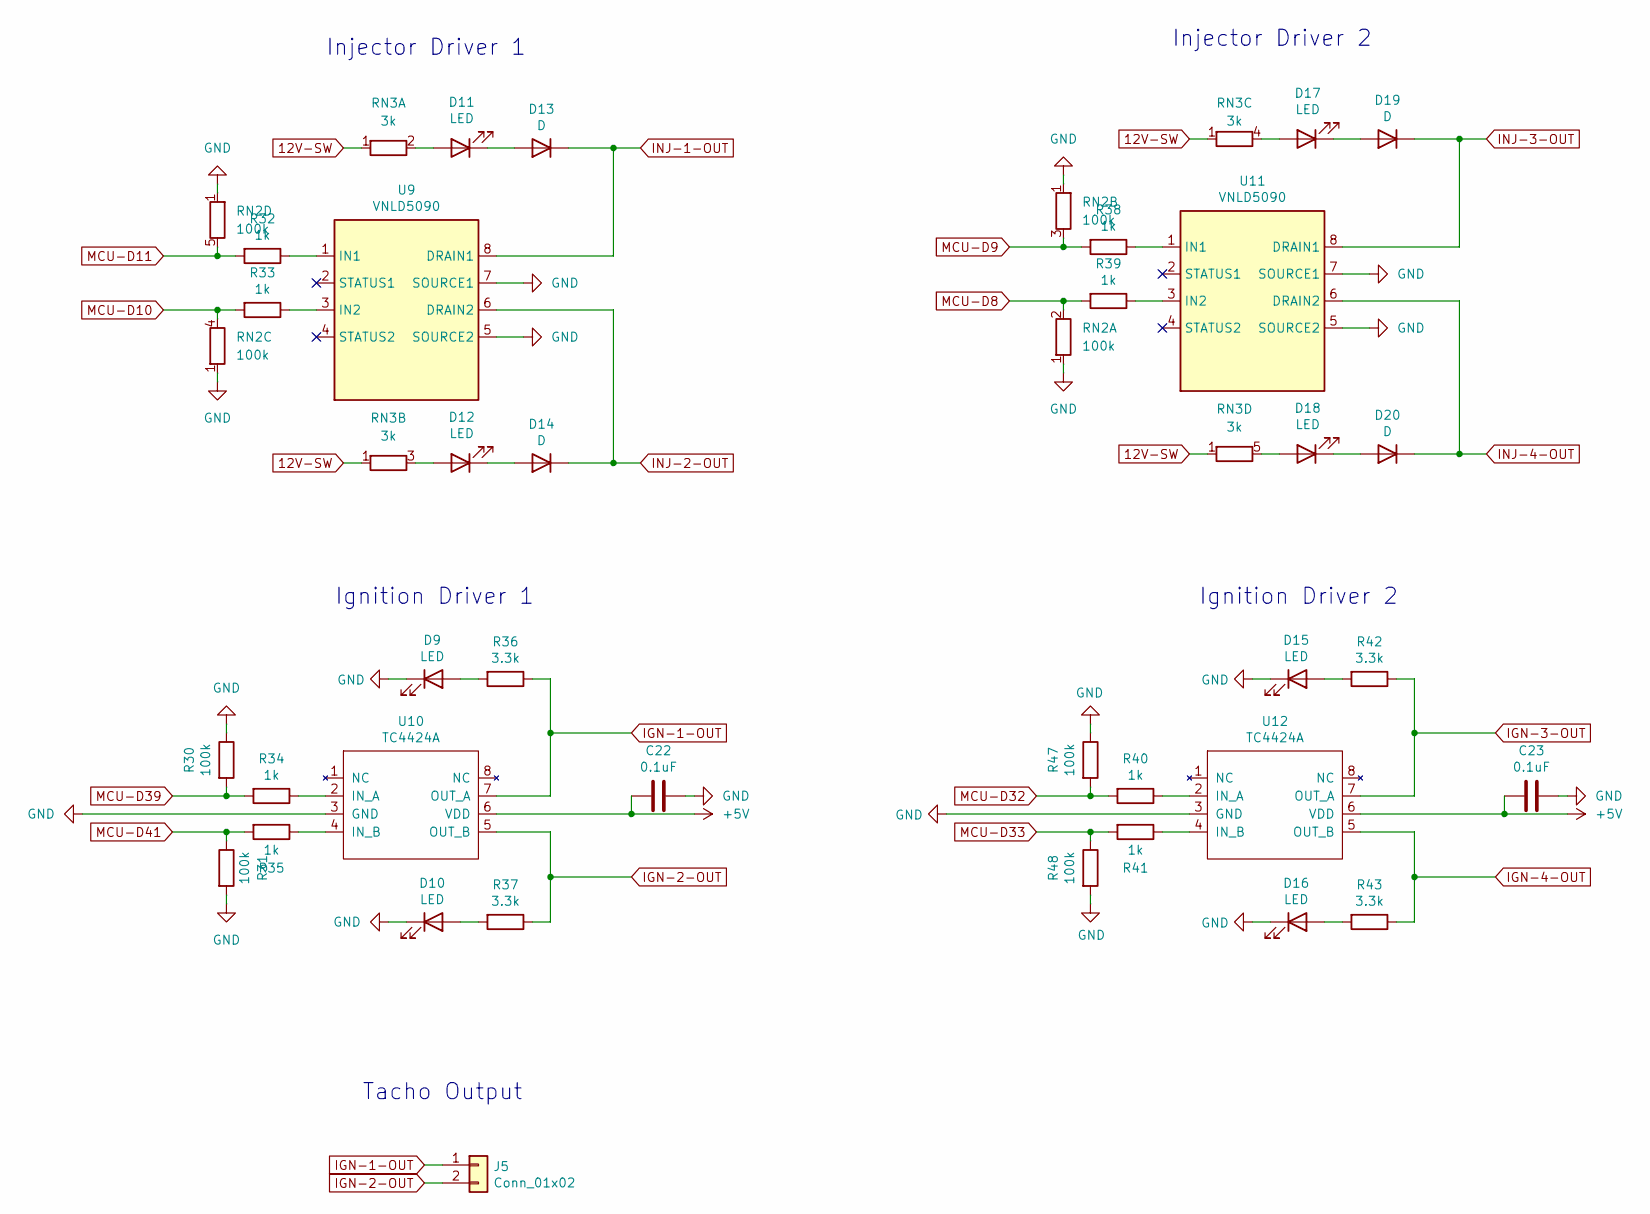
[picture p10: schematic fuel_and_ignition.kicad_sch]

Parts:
C22, C23: 0.1uF; C_Disc_D4.7mm_W2.5mm_P5.00mm; Manufacturer_Part_Number CC0805KRX7R9BB104; Digikey Part Number 311-1140-1-ND
D9, D10, D11, D12, D15, D16, D17, D18: LED; LED_D3.0mm; Manufacturer_Part_Number LH R974-LP-1; Digikey Part Number 475-1415-1-ND
D13, D14, D19, D20: D; D_T-1_P5.08mm_Horizontal; Manufacturer_Part_Number 1N4448WX-TP; Digikey Part Number 1N4448WXTPMSCT-ND
J5: Conn_01x02; PinHeader_1x02_P2.54mm_Vertical
R30, R31, R47, R48: 100k; R_Axial_DIN0207_L6.3mm_D2.5mm_P7.62mm_Horizontal; Manufacturer_Part_Number RC0805FR-071KL; Digikey Part Number 311-1.00KCRCT-ND
R32, R33, R34, R35, R38, R39, R40, R41: 1k; R_Axial_DIN0207_L6.3mm_D2.5mm_P7.62mm_Horizontal; Manufacturer_Part_Number RC0805FR-071KL; Digikey Part Number 311-1.00KCRCT-ND
R36, R37, R42, R43: 3.3k; R_Axial_DIN0207_L6.3mm_D2.5mm_P7.62mm_Horizontal; Manufacturer_Part_Number RC0805FR-072K4L; Digikey Part Number 311-2.40KCRCT-ND
RN2: 100k; R_Array_SIP5
RN3: 3k; R_Array_SIP5
U9, U11: VNLD5090; SO-8_3.9x4.9mm_P1.27mm; Manufacturer_Part_Number VNLD5090-E; Digikey Part Number 497-18682-ND
U10, U12: TC4424A; SOIC-8_3.9x4.9mm_P1.27mm; Manufacturer_Part_Number TC4424AVOA; Digikey Part Number TC4424AVOA-ND

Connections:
12V-SW: RN3.1 (R1); also elsewhere on the board
+5V: C22.2, C23.2, U10.6 (VDD), U12.6 (VDD); also elsewhere on the board
GND: C22.1, C23.1, D9.1 (K), D10.1 (K), D15.1 (K), D16.1 (K), R30.1, R31.2, R47.1, R48.2, RN2.1 (R1), U9.5 (SOURCE2), U9.7 (SOURCE1), U10.3 (GND), U11.5 (SOURCE2), U11.7 (SOURCE1), U12.3 (GND); also elsewhere on the board
IGN-1-OUT: J5.1, R36.1, U10.7 (OUT_A); also elsewhere on the board
IGN-2-OUT: J5.2, R37.1, U10.5 (OUT_B); also elsewhere on the board
IGN-3-OUT: R42.1, U12.7 (OUT_A)
IGN-4-OUT: R43.1, U12.5 (OUT_B)
INJ-1-OUT: D13.1 (K), U9.8 (DRAIN1); also elsewhere on the board
INJ-2-OUT: D14.1 (K), U9.6 (DRAIN2); also elsewhere on the board
INJ-3-OUT: D19.1 (K), U11.8 (DRAIN1); also elsewhere on the board
INJ-4-OUT: D20.1 (K), U11.6 (DRAIN2); also elsewhere on the board
MCU-D8: R39.2, RN2.2 (R1.2); also elsewhere on the board
MCU-D9: R38.2, RN2.3 (R2.2); also elsewhere on the board
MCU-D10: R33.2, RN2.4 (R3.2); also elsewhere on the board
MCU-D11: R32.2, RN2.5 (R4.2); also elsewhere on the board
MCU-D32: R40.2, R47.2; also elsewhere on the board
MCU-D33: R41.2, R48.1; also elsewhere on the board
MCU-D39: R30.2, R34.2; also elsewhere on the board
MCU-D41: R31.1, R35.2; also elsewhere on the board
unnamed: D9.2 (A), R36.2
unnamed: D10.2 (A), R37.2
unnamed: D11.2 (A), RN3.2 (R1.2)
unnamed: D11.1 (K), D13.2 (A)
unnamed: D12.2 (A), RN3.3 (R2.2)
unnamed: D12.1 (K), D14.2 (A)
unnamed: D15.2 (A), R42.2
unnamed: D16.2 (A), R43.2
unnamed: D17.2 (A), RN3.4 (R3.2)
unnamed: D17.1 (K), D19.2 (A)
unnamed: D18.2 (A), RN3.5 (R4.2)
unnamed: D18.1 (K), D20.2 (A)
unnamed: R32.1, U9.1 (IN1)
unnamed: R33.1, U9.3 (IN2)
unnamed: R34.1, U10.2 (IN_A)
unnamed: R35.1, U10.4 (IN_B)
unnamed: R38.1, U11.1 (IN1)
unnamed: R39.1, U11.3 (IN2)
unnamed: R40.1, U12.2 (IN_A)
unnamed: R41.1, U12.4 (IN_B)

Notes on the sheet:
Tacho Output
Injector Driver 2
Ignition Driver 1
Injector Driver 1
Ignition Driver 2

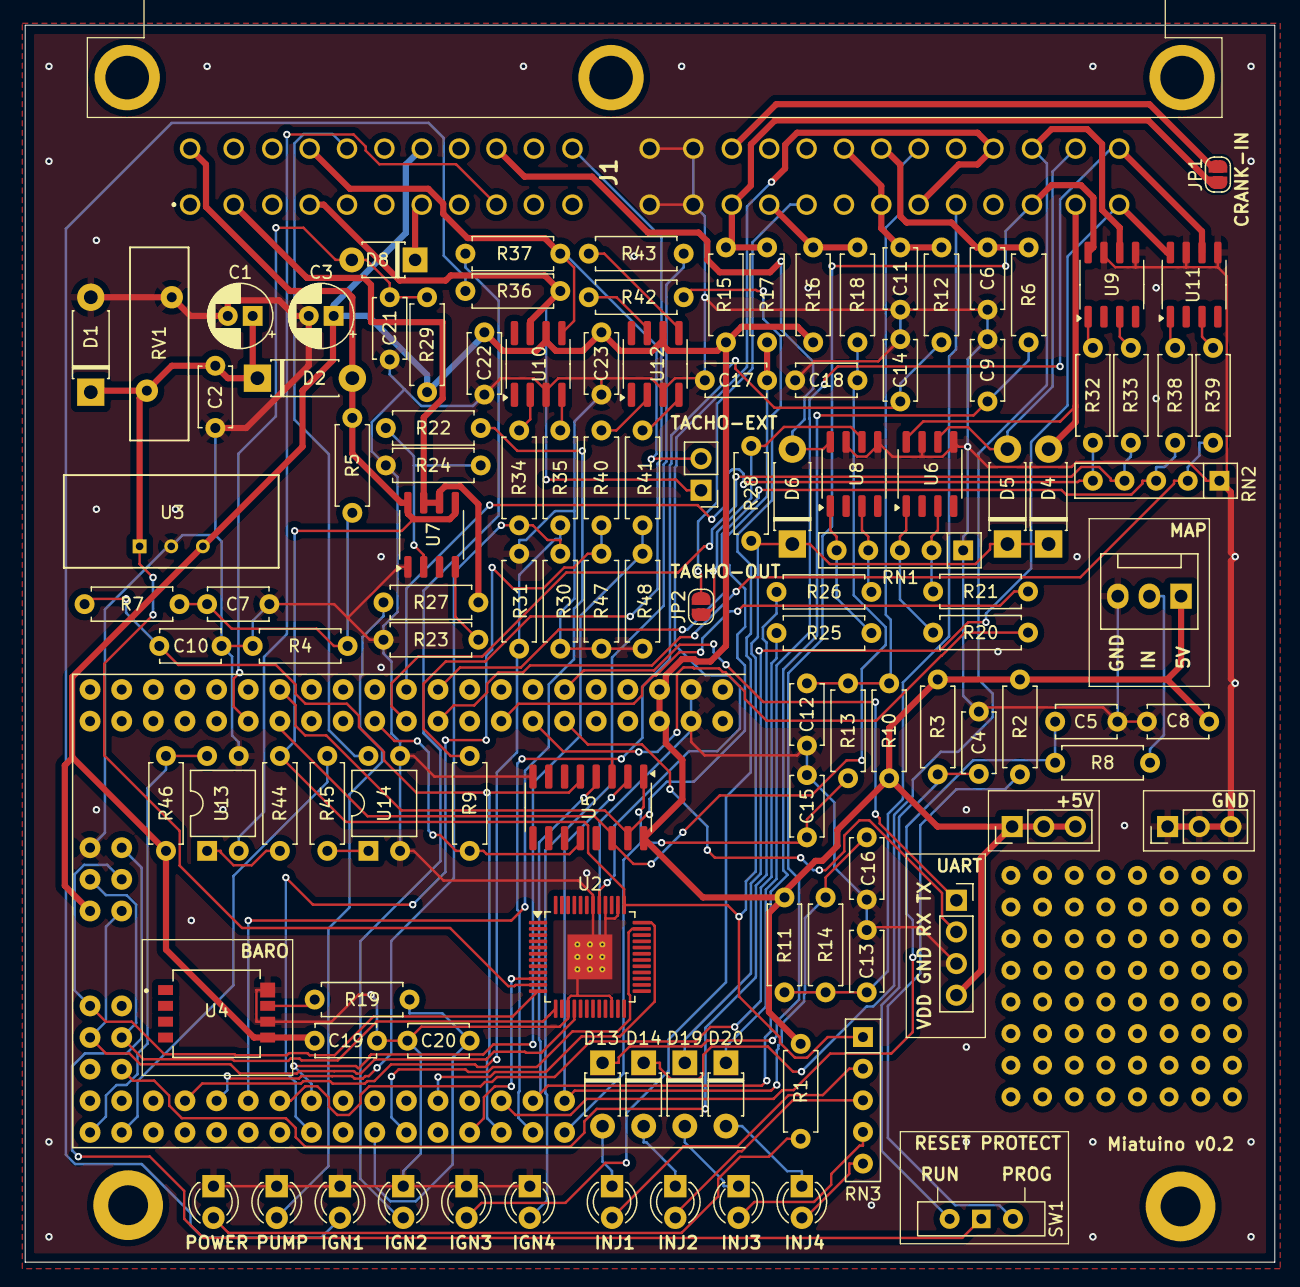
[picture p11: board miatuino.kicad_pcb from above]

Board: 2 copper layers, 100.3 x 99.3 mm, 120 parts (0 on the bottom side), 100 nets.
